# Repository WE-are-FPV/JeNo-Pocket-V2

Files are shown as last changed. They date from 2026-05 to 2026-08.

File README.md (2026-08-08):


> [!NOTE]
> Current version : **2.1.0** (read [changelog](#changelog) for details)

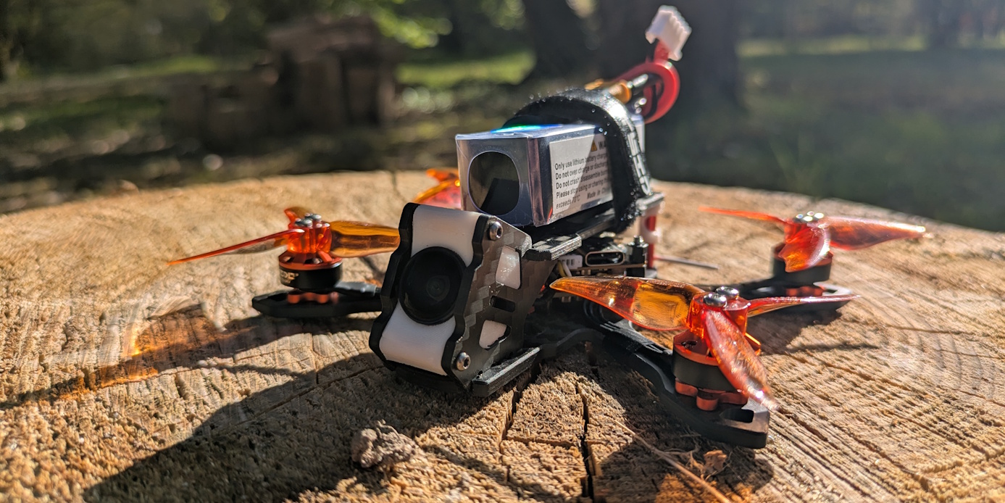
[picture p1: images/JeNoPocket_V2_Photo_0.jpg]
JeNo Pocket V2 - In the hand


# JeNo Pocket V2 2.5"
***2.5" drone FPV frame compatible with Air Unit O4 Lite (or any Nano camera), designed for Freestyle, Freeride and Cinematic.***

> [!NOTE]
> Designed in France by members of the [WE are FPV](https://www.wearefpv.fr/) community, the JeNo is already flown by hundreds of pilots and is now being sold by [Drone FPV Racer](https://www.drone-fpv-racer.com/recherche?controller=search&s=JeNo+5.1+frame&aff=64&id_campaign=13) (affiliate link). The French version of the project is available on [Printables](https://www.printables.com/model/1175339-jeno-pocket-drone-frame). Note that a [3-3.5" version](https://github.com/WE-are-FPV/JeNo-3-3.5), a [5.1-6" version](https://github.com/WE-are-FPV/JeNo-5.1) and a [7-8" version](https://github.com/WE-are-FPV/JeNo-7) of the JeNo exist.

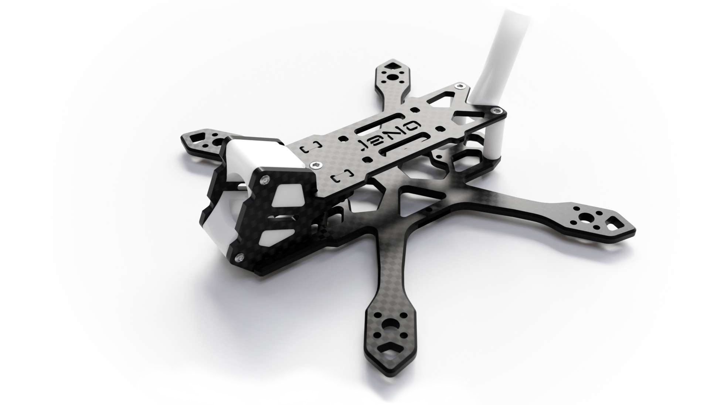
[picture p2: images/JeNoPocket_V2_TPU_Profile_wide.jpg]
JeNo Pocket V2 - 3D render


## Table of contents

* [Key features](#key-features)
* [Presentation](#presentation)
* [Detailed specifications](#detailed-specifications)
* [What’s new compared to the V1](#whats-new-compared-to-the-v1)
* [DJI O4 Wide camera plates](#Camera-plates-dji-o4-wide)
* [Recommended configuration](#recommended-configuration)
* [Versions and files](#versions-and-files)
* [Get it cut !](#buy-it-or-cut-it-)
* [Bill of materials](#bill-of-materials)
* [Building/Assembly guide](#buildingassembly-guide)
* [Inspiration](#inspiration)
* [Tuning, Betaflight Preset](#tuning-betaflight-preset)
* [Blackbox](#blackbox)
* [Videos](#videos)
* [Builds examples](#builds-examples)
* [Authors](#authors)
* [TPU](#tpu)
* [Community (remixes and TPU)](#community-remixes-and-tpu)
* [Changelog](#changelog)

## Key features
- [x] Perfect integration of the DJI **O4 Lite/Wide Air Unit** camera
- [x] Compatible with **O3 lens mods (Khrom’s mod), and O4 Wide lens mods from Flywoo/Runcam**
- [x] **Wide-X** geometry
- [x] Excellent flight **performance**, easy to tune
- [x] **Strong** and **stiff**
- [x] **Frame, standoffs and props are invisible** in the video feed
- [x] **Camera tilt options** : 15, 20, 25, 30 and 35°
- [x] **Bus height options** : 14, 16, 18 and 20 mm
- [x] Designed for: DJI O4 Lite/Wide Air Unit (**+ mods**), Walksnail Avatar/Ascent, Artlynk, HDZero and analog setups
- [x] **Easy to build**, ideal for beginners
- [x] LiPo strap slots
- [x] Compatible with flight controllers featuring a vertical USB port (with the “X-Core” and “Tank” versions)
- [x] **Open source**, of course

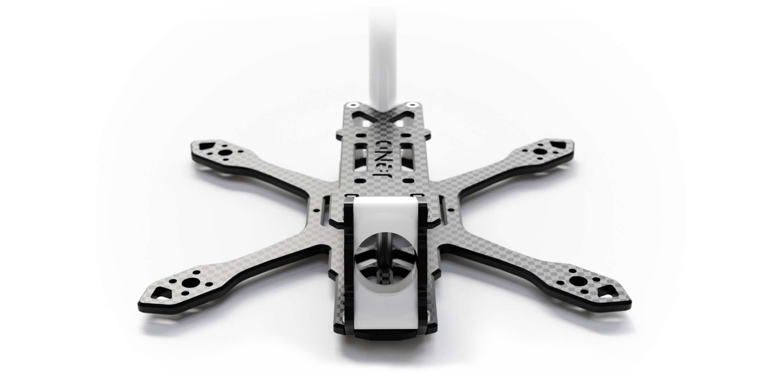
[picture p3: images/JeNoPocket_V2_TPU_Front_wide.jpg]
JeNo Pocket V2 - 3D render Front


## Presentation
In **2025/2026**, we’ve seen a few interesting new developments in the **HD VTX** world: **lens mods** for the DJI O4 Lite, BetaFPV’s **ArtLynk**, and Caddx’s **Ascent**. These evolutions are especially beneficial for compact drones, starting with the 2.5" format.

We are convinced that **2.5" is becoming a major option in FPV**, just like 5" has been for more than a decade, thanks to its many advantages: durability, discretion, lower risk, compact size, reduced manufacturing and consumable costs, ease of building, and more. It is also probably one of the **best options to get started in FPV** !

Following the success of the [first version of the JeNo Pocket](https://github.com/WE-are-FPV/JeNo-Pocket), and with the arrival of [O3 and O4 Wide lens mods](https://www.youtube.com/watch?v=6qGIw0IEMis), which finally give the **DJI O4 Lite a proper FOV**, we wanted to offer the **ultimate version** of the smallest JeNo. Here’s what’s on the menu for the **JeNo Pocket V2** :

* Updated, modern **design**
* Reinforced **durability**
* Compatibility with O4 Lite **lens mods**
* Dedicated camera plates for the new DJI O4 Wide (which replaces the O4 Lite)
* More options, so every pilot can find the setup that suits them:
  * Camera **tilt** options: 15, 20, 25, 30 or 35°
  * Bus **height** options: 14, 16, 18 or 20 mm
  * **LiPo strap** slots
  * Support for flight controllers with **vertical USB port**

Of course, this V2 keeps everything that defines the **JeNo DNA** :

* Carbon camera cage
* High performance and durability
* Completely clear video feed, with no frame or props in view
* Spacious and easy to build
* Open source

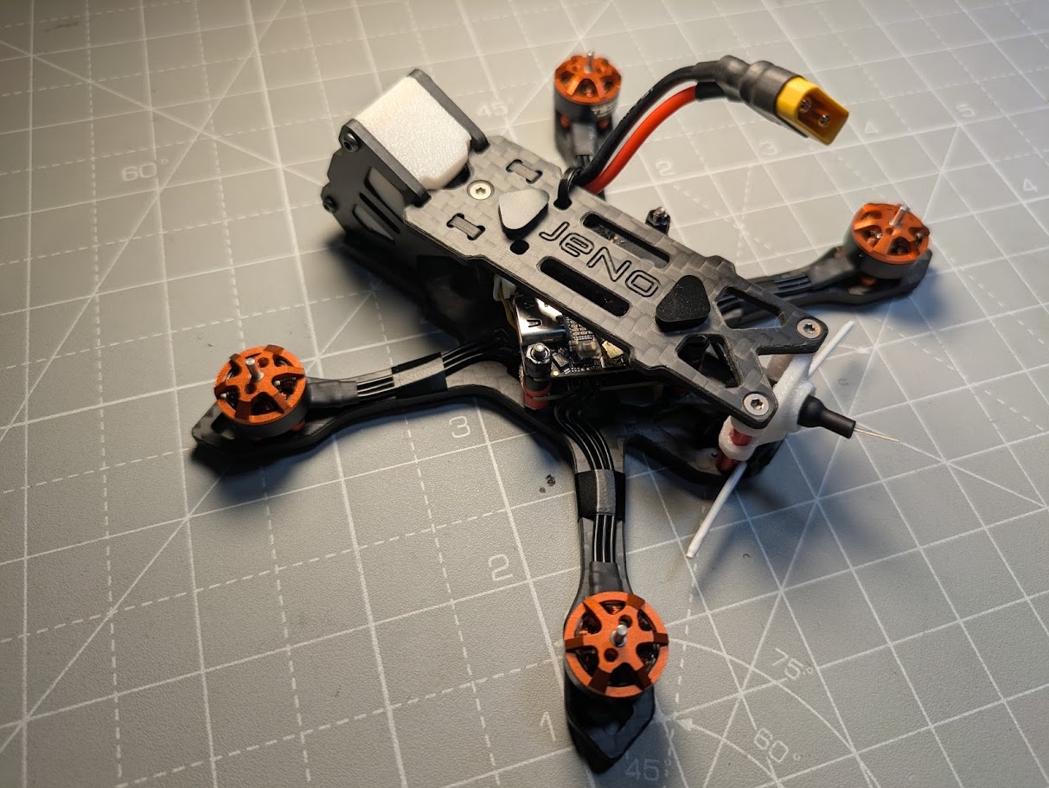
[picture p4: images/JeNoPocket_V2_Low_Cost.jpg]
JeNo Pocket V2 - Back view


This V2 is heavily inspired by [Cam.Traveler](https://www.printables.com/@Cam_Traveler_2489307)’s [JeNo 25](https://github.com/WE-are-FPV/JeNo-Pocket), which itself was inspired by the [JeNo Pocket](https://www.printables.com/model/1175339-jeno-pocket-drone-frame) and [JeNo Fit 3"](https://github.com/WE-are-FPV/JeNo-Fit-3-3.5). Huge thanks to him for his work and for sharing it. Once again, this shows the benefits of open source, where everyone gets to benefit.

## Detailed specifications

|||
| :--- | :--- |
| **Geometry** | **Wide-X** | 
| **Props size** | 2.5" | 
| **Weight** | **X-Core : 25 g**, **Classic : 27 g**, **Tank : 30 g** (with screws) | 
| **Body height** | 14/16/18/20 mm | 
| **Bottom plate** | 3 mm | 
| **Top plate** | 2 mm | 
| **Camera plates** | 2 mm | 
| **Motors mounting** | 9 mm | 
| **Camera** | 14 mm (Nano), O4 Lite and mods, **Clear FOV**. |
| ** Camera tilt** | 15/20/25/30/35° |
| **Main stack** | 25.5 mm x 25.5 | 
| **Back stack** | RX area. 13 mm x 13 mm | 
| **Supported VTX** | Analogic, **DJI Air Unit O4 Lite/Wide (+mods)**, WalkSnail Avatar/AScent, HDZero, ArtLynk… | 
| **Strap passage** | Yes | 

## What’s new compared to the V1

### Redesign and durability

Since the [JeNo Fit 3"](https://github.com/WE-are-FPV/JeNo-Fit-3-3.5), we’ve been trying to move away from the standard stack-area design, with its classic side “spikes”, and adopt **more harmonious shapes** instead. This improves both the look and the **durability**, with wider arm bases that are therefore stronger and more rigid.

Here is an overview of the main differences between the V1 and the V2. The center patterns have been removed for this comparison, so we can focus on the main structure.

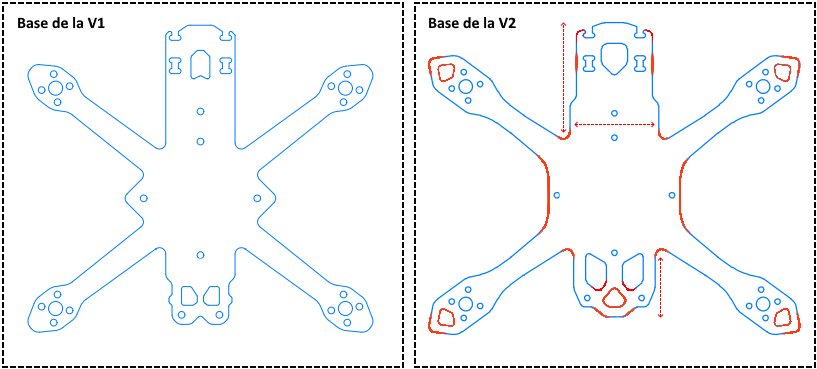
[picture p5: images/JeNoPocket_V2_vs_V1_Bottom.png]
JeNo Pocket V2 - V1 vs V2


The red areas highlight the main changes. Beyond the **more visually appealing design**, the arms appear shorter — and they actually are! Removing the side spikes in favor of a direct junction between the arms and the bus **significantly reinforces the arms**.

There are also a few other improvements worth highlighting:

* Better **motor protection** at the end of the arms
* **The front** of the bottom plate has been **widened and shortened for better durability**. There is also more material between the slots for the camera plates and the edge of the frame.
* **The rear** has also been shortened
* Mounting support for a T-style antenna
* As we will see later, cutouts are also provided for flight controllers with a **vertical USB port**.

The following image shows an overlay of the V1 and V2 to better illustrate the differences.

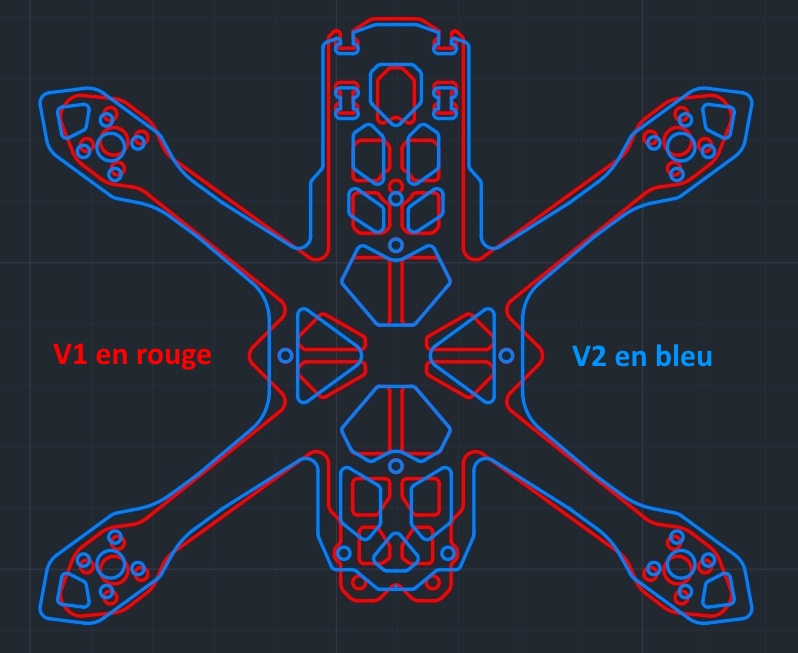
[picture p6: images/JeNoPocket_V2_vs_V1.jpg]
JeNo Pocket V2 - V1 vs V2 over


### "À la carte" bottom plate options

We offer **3 versions** of the bottom plate, all based on the improvements mentioned above.

The **V2 “Classic”** bottom plate is the direct evolution of the **V1** : it features a carbon cross in the center, ensuring good rigidity across all axes. Like the V1, it also **does not include** a cutout for flight controllers equipped with a **vertical USB port**.

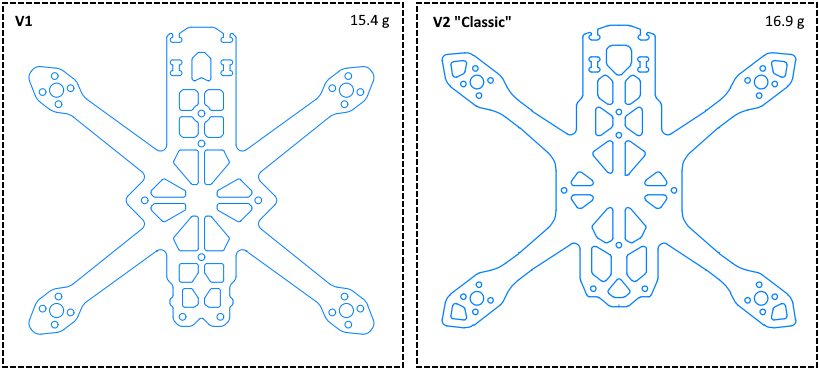
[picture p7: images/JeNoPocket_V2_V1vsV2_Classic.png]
JeNo Pocket V2 - V1 vs V2 Classic


*Two other versions** are also available, both **compatible** with flight controllers equipped with a **vertical USB port** :

* **V2 “X-Core”** : this is the optimized version of the JeNo Pocket V2. Lighter than the “Classic” and more durable than the V1, it is characterized by a **carbon X in the center**, following the diagonals of the arms. **Ideal with lightweight props** such as the Gemfan 2520. It is less tolerant of heavy props that generate a lot of vibrations, such as the Avan Rush.

* **V2 “Tank”** : with its **wider arms** and “solid” carbon layout, this is the **stiffest and most durable** of the 3 versions. We did not call it V2 “Bando” because, in absolute terms, all 3 versions remain strong enough for that kind of flying.

At **4.7 g heavier** than the **“X-Core”** version, it is also **more tolerant** of heavy or high-pitch props during hard full-throttle punches.

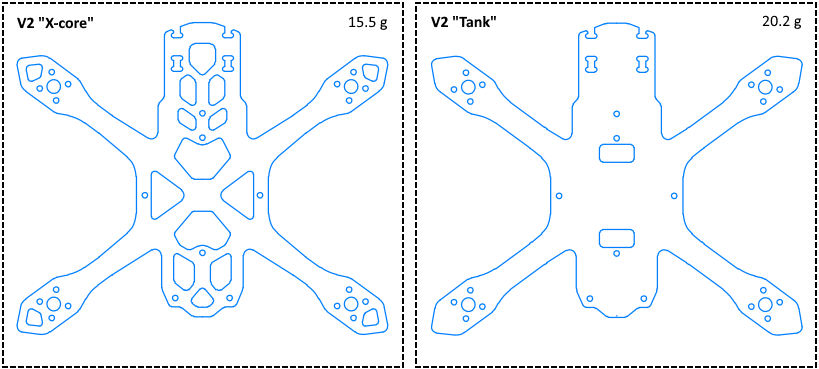
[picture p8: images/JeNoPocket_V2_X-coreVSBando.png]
JeNo Pocket V2 - X-Core vs Tank


Example build with a flight controller equipped with a vertical USB port:

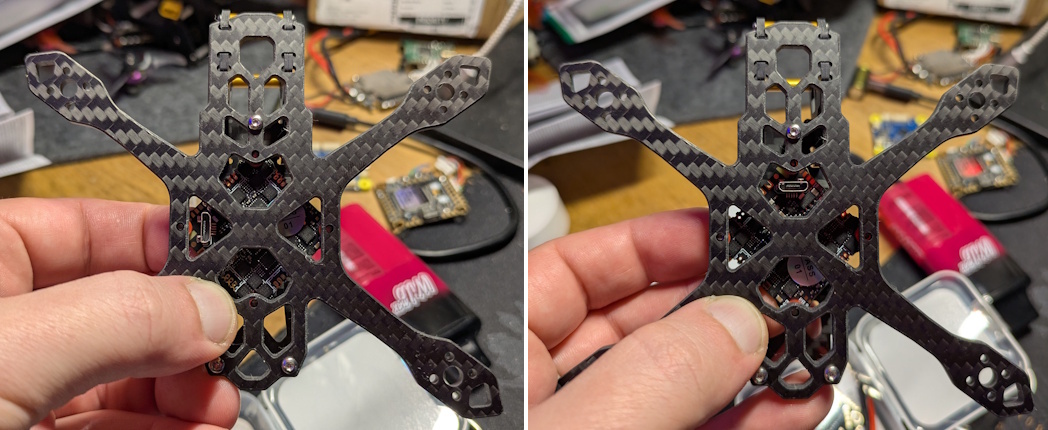
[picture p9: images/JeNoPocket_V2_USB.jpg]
JeNo Pocket V2 - vertical USB


### Customizable camera plates : height and tilt

The **single bus height** of the **V1**, 20 mm, was convenient because it was spacious and even allowed for a Naked Vista build, but some pilots prefer a more **low-profile** bus. It is now possible to **choose the height** :

* **14 mm** : very low-profile, but be careful, the build will be more difficult
* **16 mm** : a good compromise, making the build easier while staying relatively low profile — Nochamo’s preference
* **18 mm** : allows for an easy build without going all the way up to 20 mm — Jérôme’s preference
* **20 mm** : still available for maximum space and Naked Vista compatibility

We recommend the two intermediate versions: 16 or 18 mm.

Camera tilt is now also optional: the camera plates are available in **15, 20, 25, 30 or 35°**.

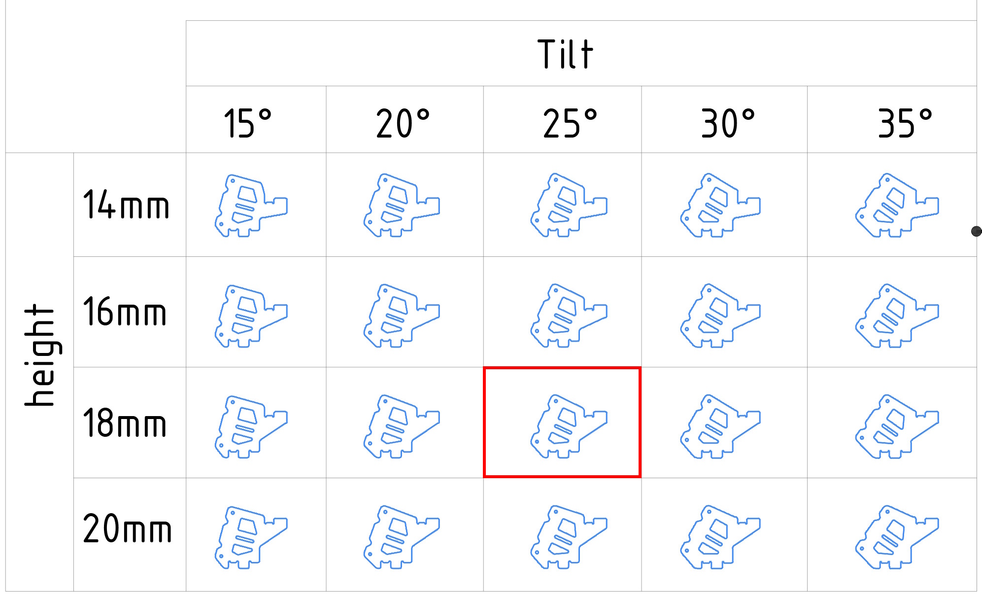
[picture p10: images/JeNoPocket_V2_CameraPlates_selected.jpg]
JeNo Pocket V2 - Camera plates


As an example, in the image above, the version highlighted in red is the one to choose for an 18 mm bus height and a 25° camera tilt.

### Camera plates DJI O4 Wide

The **JeNo Pocket V1 and V2** were designed, in part, around the **DJI O4 Lite**. Unfortunately, it is **no longer available** and has been replaced by the **DJI O4 Wide**. While the VTX itself is identical, the camera—particularly the lens and its mounting system—is different.

The larger size of the new DJI O4 Wide camera required us to design a new set of **dedicated** camera plates.

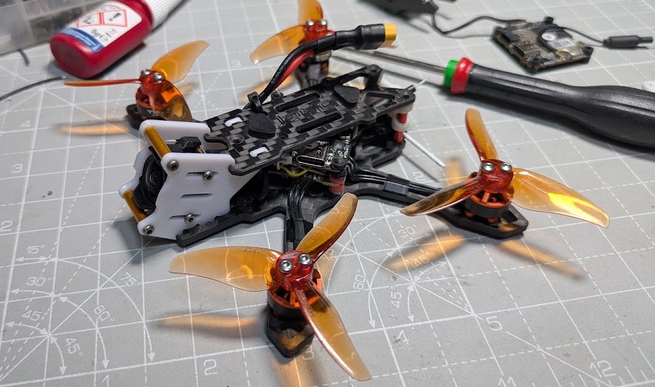
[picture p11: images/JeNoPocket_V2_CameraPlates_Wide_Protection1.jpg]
JeNo Pocket V2 - DJI O4 Wide


We could have replaced the standard camera plates with these new ones, but we chose not to compromise the design for all the other cameras just to accommodate the constraints of the O4 Wide. You will therefore be able to choose between **two types of camera plates** for the JeNo Pocket V2:

* **Standard** model: this is the original version and the one we recommend for **ALL** cameras **except** the DJI O4 Wide camera. Even when using a DJI O4 Lite with an **O3 lens mod**, this is the model you should choose.
* **DJI O4 Wide** model: this version should **only** be used with the DJI O4 Wide. Its main advantage is that it does not require any TPU mount: the camera is screwed directly onto the camera plates. No modification or workaround is needed—it can be installed straight out of the box. The downside is that the plates are slightly larger and consist of separate left- and right-hand parts.

The illustration below will help you visualize the difference in size.

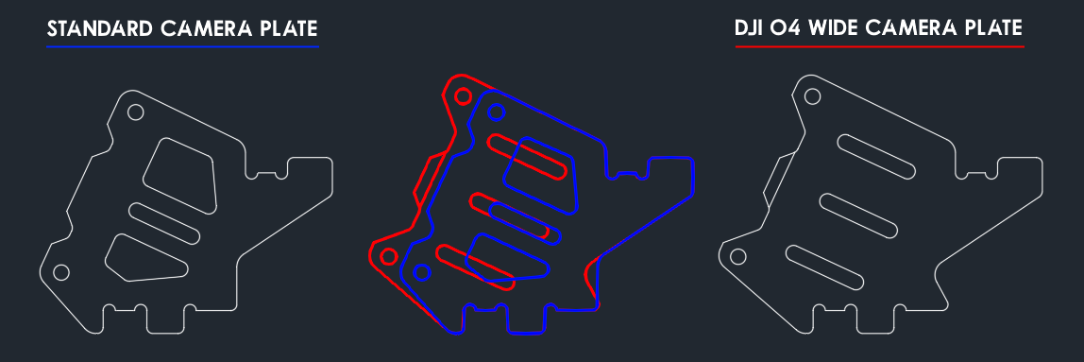
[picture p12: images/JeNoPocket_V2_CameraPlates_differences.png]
JeNo Pocket V2 - DJI O4 Wide differences


To provide the **best possible protection** for the DJI O4 Wide lens while keeping its **FOV** completely **unobstructed**, we had to add **chamfers** to the central section. This means using two different, mirrored plates for the left and right sides.

We would like to draw **carbon manufacturers’** attention to the precision of these chamfers. They are **essential** to allow the camera to be positioned as far back as possible.

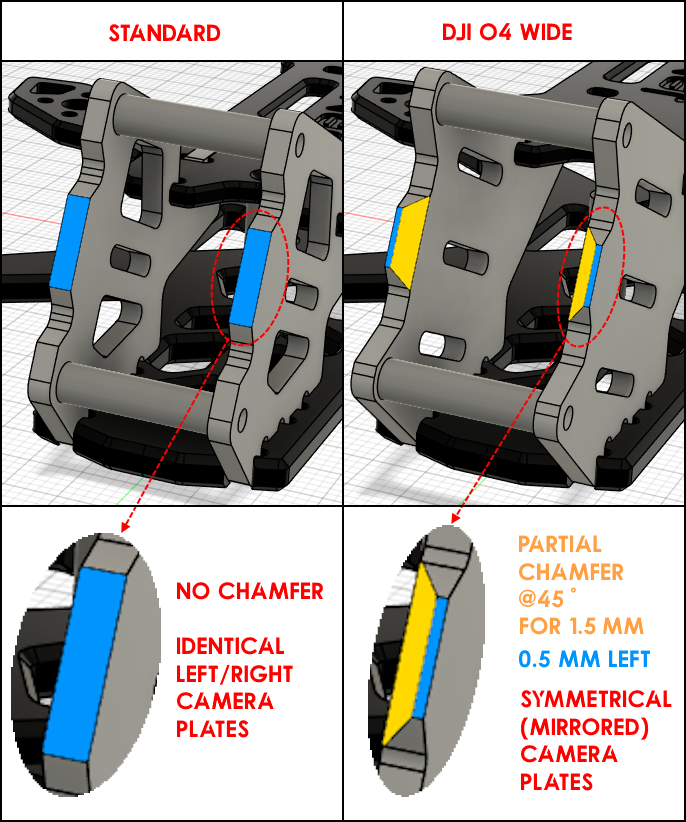
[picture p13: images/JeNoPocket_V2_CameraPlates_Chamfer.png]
JeNo Pocket V2 - DJI O4 Wide chamfers


The camera must be moved forward precisely to the beginning of the chamfer, as shown in the photo below.

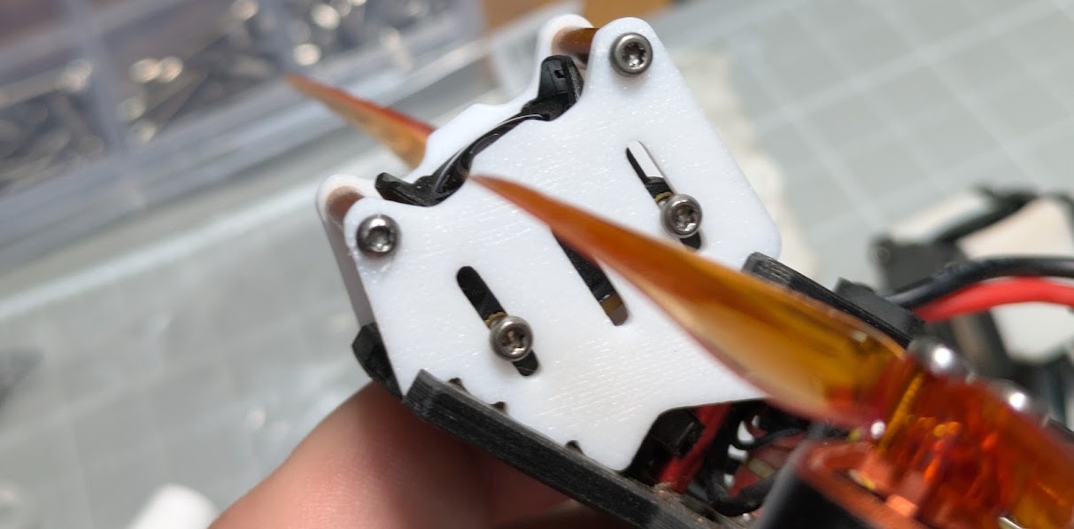
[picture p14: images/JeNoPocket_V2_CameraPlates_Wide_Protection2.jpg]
JeNo Pocket V2 - DJI O4 Wide placement


This ensures optimal protection.

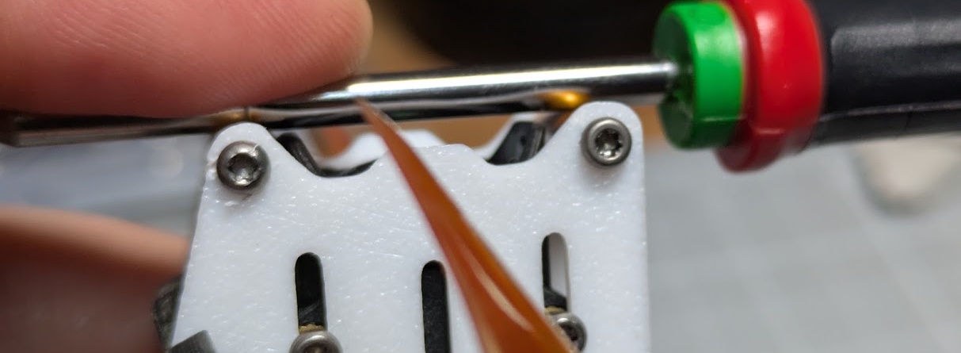
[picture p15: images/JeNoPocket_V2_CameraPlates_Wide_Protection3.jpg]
JeNo Pocket V2 - DJI O4 Wide placement


### Top plates

The top plate remains fairly simple, with the addition of **slots for a LiPo strap**.

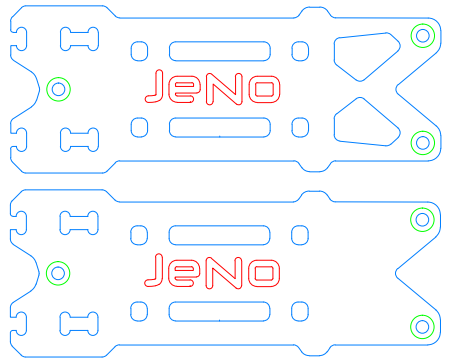
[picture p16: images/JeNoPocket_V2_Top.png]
JeNo Pocket V2 - Top plate


The **two small holes** above and below the “J” are intended to secure the **pigtail** with a **zip tie**.

Given the size of the frame, the “JeNo” engraving is quite fine. If your carbon cutter is not able to machine the logo as a **pocket**, it is still possible to **engrave only the outline** — it also looks very nice.

The space on both sides of the logo can be used to install small **LiPo pads**.

JeNo Pocket V2 - LiPo Pads

A **reinforced version** of the top plate is also available for the **“Tank”** version.

### Camera mounts

For standard **Nano-sized** cameras, with one screw hole on each side, mounting is done directly through the central rail of the camera plates, allowing you to adjust the camera setback as needed.

| Standard nano camera | O3 Lens Mod |
| :---: | :---: |
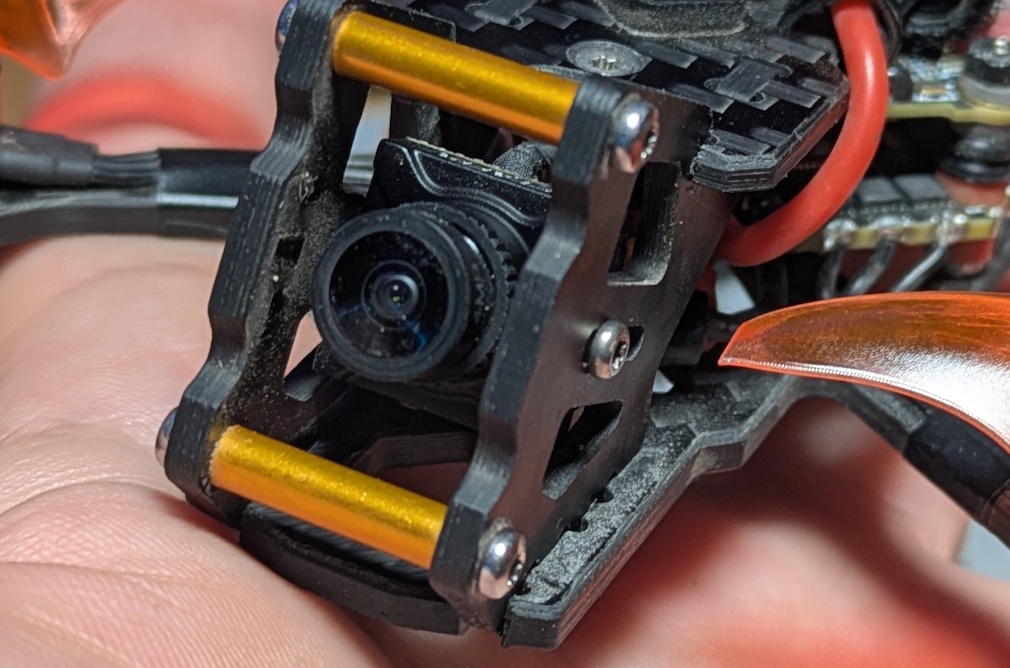
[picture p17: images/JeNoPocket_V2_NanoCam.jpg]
JeNo Pocket V2 - Standard nano camera
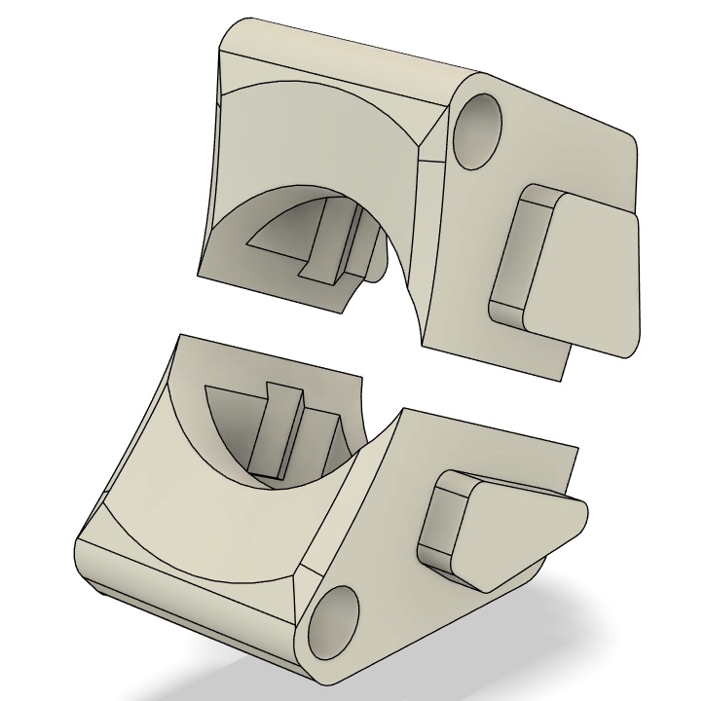
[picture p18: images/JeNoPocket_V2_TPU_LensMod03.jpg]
JeNo Pocket V2 - O3 Lens Mod
|  |  |

For the O4 Lite camera, we designed two-piece TPU mounts that wrap around the camera and are locked in place by the camera plates. Three TPU mounts are available:

A standard version for the unmodified O4 Lite camera
A version for the O3 lens mod — the best conversion currently available
A version for the Flywoo/Runcam O4 Wide lens mod

To get a **fully unobstructed FOV**, move the lens about one millimeter forward past the TPU, as shown in the image above. Conversely, for more protection, you can move the camera very slightly backward, at the cost of very minor vignetting.

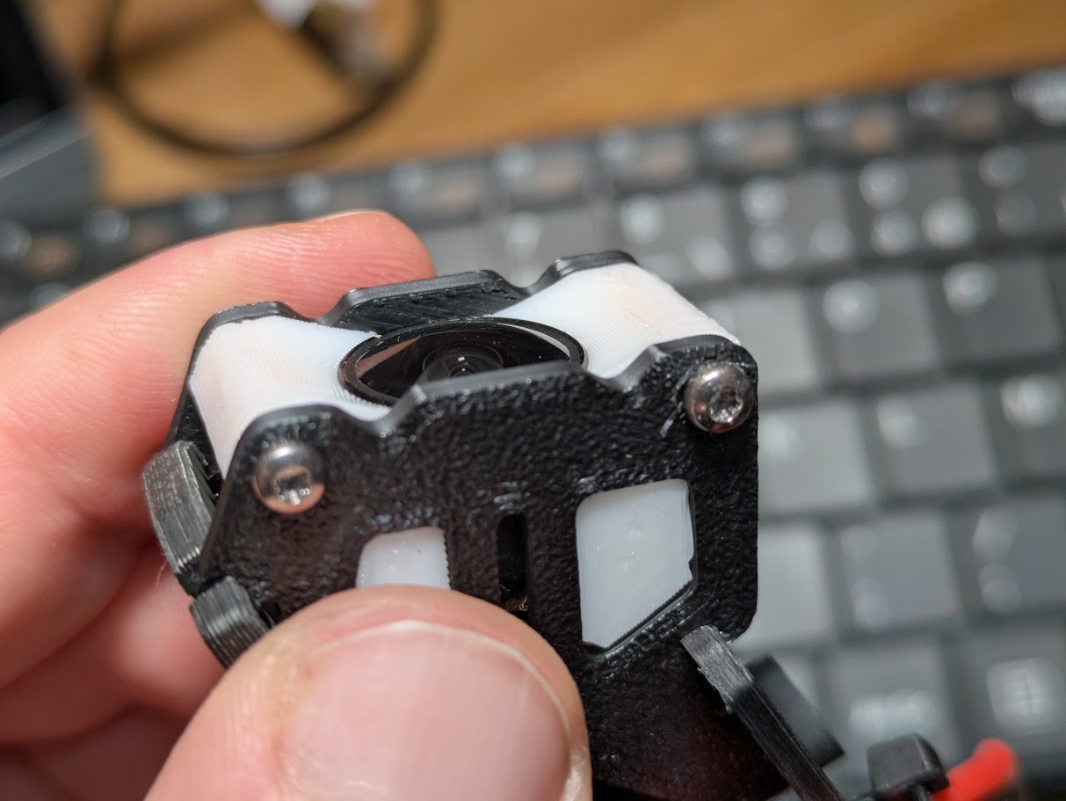
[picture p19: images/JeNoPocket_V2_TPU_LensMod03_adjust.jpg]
JeNo Pocket V2 - O4 Lite mods


These TPU parts are designed to integrate perfectly with the carbon. However, depending on cutting tolerances and leftover TPU support material, a few small adjustments with flush cutters may be required for the TPU to fit properly.

## Recommended configuration

Different approaches are possible, from ultra-light to mini-rocket, depending on your hardware choices.

### Motors

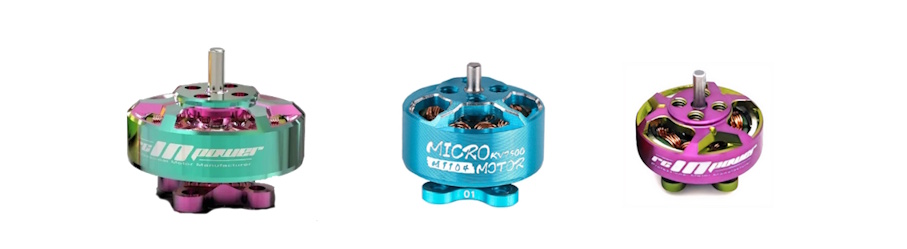
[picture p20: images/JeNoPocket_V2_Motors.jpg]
JeNo Pocket V2 - Motors


| **Size** | **Stator volume** | **Recommended KV (2S)** | **Recommended KV (3S)** |
| :---: | :---: | :---: | :---: |
| 1202 | 226 mm³ | ~8000 | ~6000 |
| 1103 | 285 mm³ | ~8000 | ~6000 |
| **1203** | **339 mm³** | **~8000** | **~6000** |
| **1104** | **380 mm³** | **~8000** | **~6000** |
| **1303** | **398 mm³** | **~8000** | **~6000** |
| 1204 | 452 mm³ | ~8000 | ~6000 |
| 1105 | 475 mm³ | ~8000 | ~6000 |

2S motors can also be used on 3S thanks to **Betaflight’s Motor Limit** feature. In fact, this is probably the best approach: choosing motors around **7500–8000 KV** allows you to run them on both 2S and 3S.

These small motors, such as the **RCInPower** 1203 8000KV or **BetaFPV** 1104 7500KV, are still quite expensive despite their size. A low-cost option is available from [**YSIDO** with their 1104 7500KV motors](https://fr.aliexpress.com/item/1005005729701162.html), which can usually be found for around €20–25 for a set of 4. For bando flying, they probably won’t be the most durable option, but for freestyle, they do the job very well.

### Lipos

We recommend **2S or 3S lipos** as indicated in the table above, although 4S is also an option.

**2S ~550 mAh** lipos are a good compromise, or **3S ~450 mAh**. For maximum flight time, **3S ~550 mAh** lipos are still perfectly viable.

Small 2S ~450 mAh lipos are possible with a very light setup and small motors, but the impact on flight time and sag may become noticeable.

In any case, we strongly recommend **Dogcom 2S and 3S 560 mAh** lipos, as they have shown the best performance by far.

<p align="center">
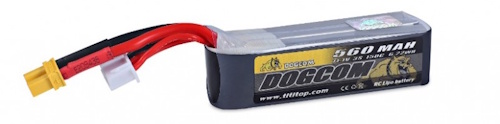
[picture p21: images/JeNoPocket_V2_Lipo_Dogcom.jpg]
  
</p>

Depending on the lipos, during a freestyle flight outdoors in cold weather (~5°C), flight times can range from **2 minutes** (BetaFPV 2S 450 mAh) to **5 minutes** (Dogcom 3S 560 mAh)! You can even hope to reach **7 minutes** with a smooth flight using these same lipos.

### Props

We tested many props from **Gemfan, HQ and Emax** for freestyle flying. The props we recommend are the **Gemfan Hurricane 2520-3** and the **HQ 2.5x1.9x3** : light, responsive and precise. They work perfectly with all bottom plate versions and make a perfect combo with the **“X-Core”** version: it is lightweight and flies very well.

The **Emax Avan Rush 2.5"**, along with other heavier or higher-pitch props, are more “brutal” due to their very **unusual profile** and **higher weight**. This is not an issue for freestyle flying, but during sustained full-throttle punches, vibrations may appear on the “X-Core” version. The **“Classic” and “Tank”** versions absorb them well.

[Here is an example of a full-throttle punch followed by freestyle flying](https://youtu.be/E_eKk1bxeOk) in 3S on the **“X-Core”** version with these **Avan Rush 2.5"**, to illustrate the behavior with these props.

We did not want to exclude them from the recommended props for the JeNo Pocket V2 for 3 reasons:

* They are the **most durable props** available. You almost never need to replace them, which is an important point, especially with T-Mount props, which are often tedious to change.
* The vibration issue does not exist on the **“Tank”** version and is anecdotal on the **“Classic”** version.
* On the “X-Core” version, it only appears during full-throttle punches. It is not a deal-breaker, but the Gemfan 2520 simply fly much better.

> [!TIP]
> **Gemfan 2520 →** ideal for **all versions** of the JeNo Pocket V2

> [!TIP]
> **Emax Avan Rush →** we recommend the **“Classic”** or **“Tank”** versions for better flight behavior, especially during full-throttle punches.

### FC, ESCs and RX
Here, you’ll have plenty of choices, as the range is very diverse. The main recommendation is to go for an **FC AiO** with ESCs that can deliver **20A**, to be on the safe side, although theoretically, 15A should be sufficient.

The O4 Lite can be powered **directly from the lipo** if you’re using 2S or 3S. For higher voltages, you'll need an FC with a BEC capable of delivering at least 10W for the O4.

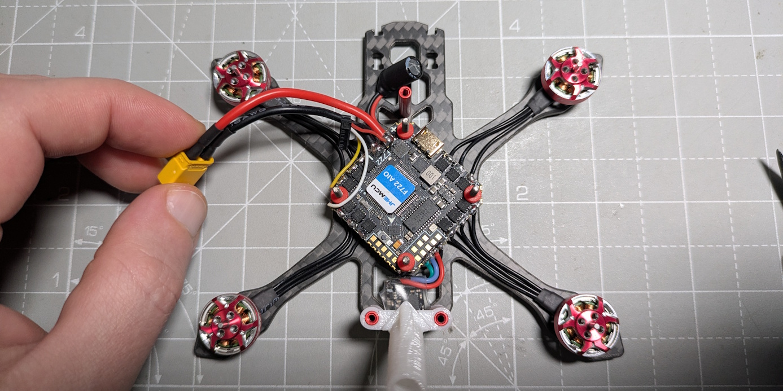
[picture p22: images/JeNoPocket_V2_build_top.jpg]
JeNo Pocket V2 - Top view


Having experienced many unreliable AiOs that didn’t meet the advertised specifications, we recommend opting for **proven hardware**.

Choosing an FC with an **integrated RX** can be a good option to save weight. When they feature a copper antenna, the range is generally quite limited. An **external RX** will often be a better option for range.

Those equipped with a flat antenna or, even better, a ceramic antenna, will offer a good balance of range while minimizing weight gain.

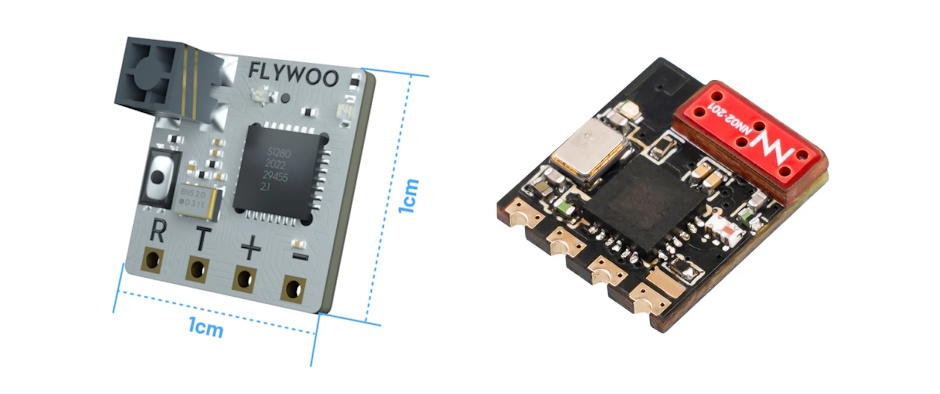
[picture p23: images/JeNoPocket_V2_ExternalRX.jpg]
JeNo Pocket V2, RX options


**Affordable and proven AiO recommendations :**

* **[JHEMCU GHF722AIO-HD 40A](https://fr.aliexpress.com/item/1005004940172936.html) :** almost overkill for a 2.5", but still a solid option with lots of positive feedback. We even use it on our 3.5" builds. However, you will need to add an external RX.

* **[JHEMCU GHF435AIO V2 20A](https://fr.aliexpress.com/item/1005007942847361.html) :** probably the perfect AiO for the JeNo Pocket. Its F435 is roughly equivalent to an F722, it is cheaper, and it also comes with an onboard RX! And this is a real RX, not an SPI receiver. It can therefore be used and flashed like a standalone RX. The cherry on top: it has a µ.FL connector, allowing you to use a proper antenna and therefore get maximum range. On this FC, the USB connector is vertical, so the **“X-Core” or “Tank”** version is required.

The **capacitor** is generally not required for 2S and 3S builds, but if you choose to use one, a **220 µF 25V** will do the job and can be placed either at the front standoff or at the back.

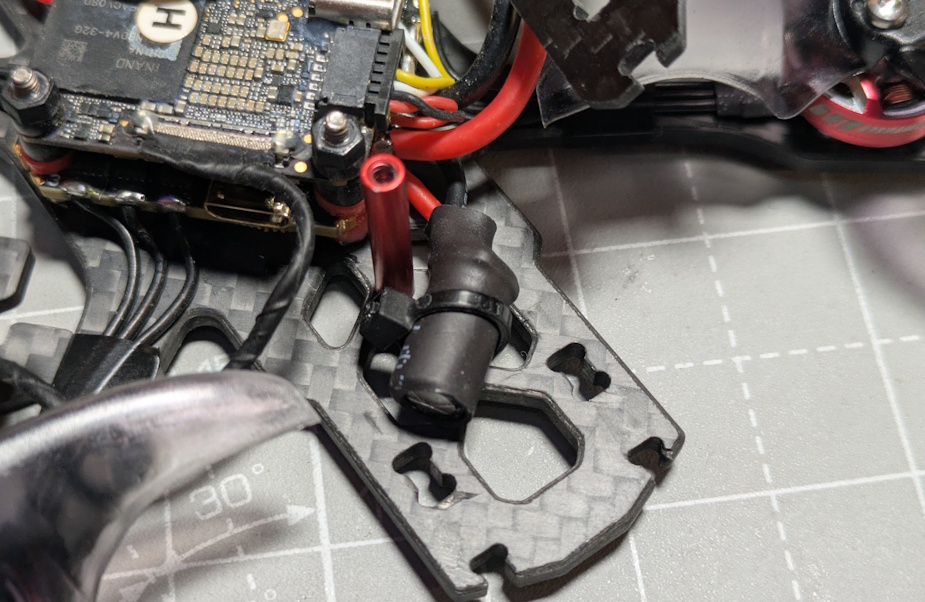
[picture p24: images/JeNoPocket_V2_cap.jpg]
JeNo Pocket V2, Capacitor


As for the **XT30** pigtail, **18 AWG** cable is a good compromise.

## Versions and files

### Versioning
You will find the **current version** of the frame at the beginning of the description and the full [history of modifications](#changelog) at the end of the page.

We strongly recommend always cutting the latest version to ensure you benefit from the most recent optimizations.

The version **number format** is as follows :
```
<Major versions>.<Minor version>.<Revision>
ex : 1.3.2
```

* **Revision :** This number is incremented in the case of minor modifications with no significant impact.
* **Minor version :** This number is incremented for minor modifications that may potentially break compatibility with certain TPU parts.
* **Major version :** This number is incremented for significant modifications that break compatibility at the carbon level.

**Note :** If you develop TPU parts for the JeNo, be sure to specify the version they are compatible with.

### Files management
To simplify things, we have reorganized the file structure. The files are now divided into **five groups** :

* **01-FRAME :** Contains **models** describing the **frame** in DXF, STEP, and STL formats for the current version. Also contains a PDF file which is a reformatted version of the DXF.
* **02-TPU :** Contains **TPU models** for the current frame version in STL format.
* **03-FRAME-HISTORY :** Contains previous versions of the frame.
* **04-TPU-HISTORY :** Contains TPU models that are no longer compatible with the current version.
* **OTHER-FILES :** Contains documentation files, including the assembly manual and a description.

## Get it cut !

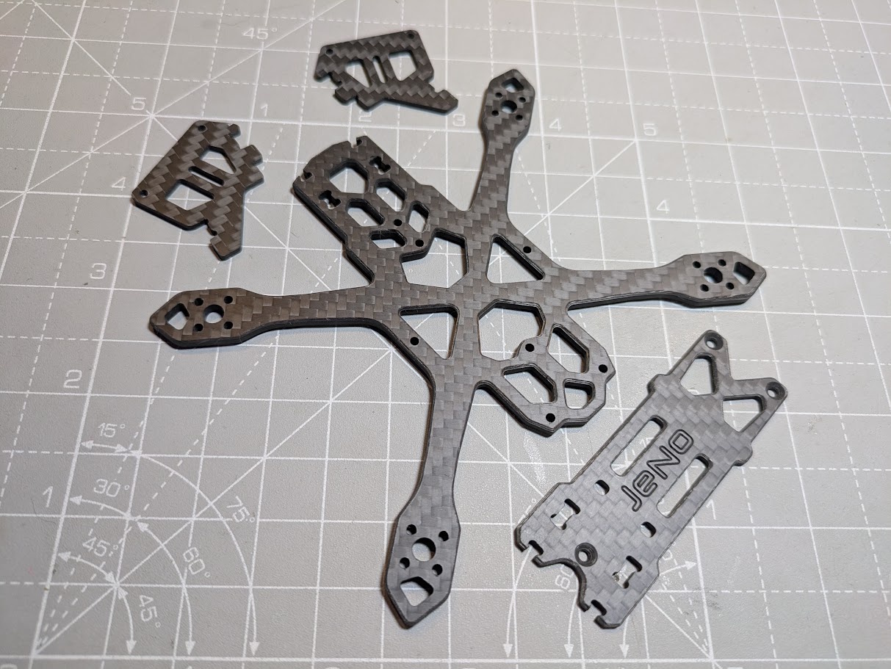
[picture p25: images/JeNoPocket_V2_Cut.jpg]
JeNo Pocket V2, cut


The JeNo Pocket V2 is available at [FPV CNC Drone](https://fpvcncdrone.com/).

The ["01-FRAME"](https://github.com/WE-are-FPV/JeNo-Pocket-V2/tree/main/01-FRAME) folder contains all the files you need to get it **cut**. .DXF and .STEP files are available.

The bottom plate must be cut from 3 mm thick carbon fiber. The top plate and camera plates should be cut from 2 mm carbon fiber.

By default, we recommend adding **chamfers everywhere, except on the camera plates**.

**One last point :** carbon cutters generally use carbon sheets made of fiber layers oriented at 0° and 90°. To achieve the best arm stiffness, the bottom plate should be **oriented at 45°** during cutting. This is something they are usually very familiar with, but we prefer to mention it.

## Bill of materials

In addition to the carbon fiber, you will need the following hardware to complete the assembly of the frame.

**Standoffs**

Important note: M2 standoffs come in two diameters: 3.5 mm and 4 mm. **Make sure to use 3.5 mm diameter standoffs** (you can optionally keep a 4 mm diameter for the central standoff.).

If you machine or manually shorten the standoffs, make sure to precisely match the bus height required for your camera plates.

| Quantity | Description | Details |
| :---: | :--- | :--- |
| **3** | **M2** standoffs, **3.5 mm diameter**. Available in 14, 16, 18 or 20 mm, depending on the selected bus height. | for the body |
| **2** | **M2x14mm** standoffs **(3.5 diameter)** | for the camera |

**Stack materials**

Titanium is lighter, but it will tend to bend over time after repeated hard crashes. This is even more noticeable with taller stacks.

| Quantity | Description | Details |
| :---: | :--- | :--- |
| **4** | **M2x20mm** screws, depending on the selected bus height: 14 mm → M2x16, 16 mm → M2x18, 18 mm → M2x20, 20 mm → M2x20 | for the stack |
| **8** | **M2** nylon nuts for the stack screws (4 nuts for the base, 4 nuts on top) | for the stack |

**Frame materials**

Don’t hesitate to apply a small amount of threadlocker to the screws to reduce the risk of them coming loose, which is fairly common on small, high-powered builds using M2 hardware.

| Quantity | Description | Details |
| :---: | :--- | :--- |
| **3** | **M2x6-8 mm** countersunk screws | for the top plate |
| **3** | **M2x8-10 mm** screws | for the bottom plate |
| **4** | **M2x6 mm** screws (titanium if possible) | for camera plates |

**Additional materials**

| Quantity | Description | Details |
| :---: | :--- | :--- |
| **12-16** | **M2x5mm** screws if there is NO arm protection between the screw and the motor, otherwise, **M2x6mm**. To save **weight**, you can use only **2-3 screws per motor**. | for the motors |

## Building/Assembly guide

### Build
The assembly of the frame is straightforward :

<p align="center">
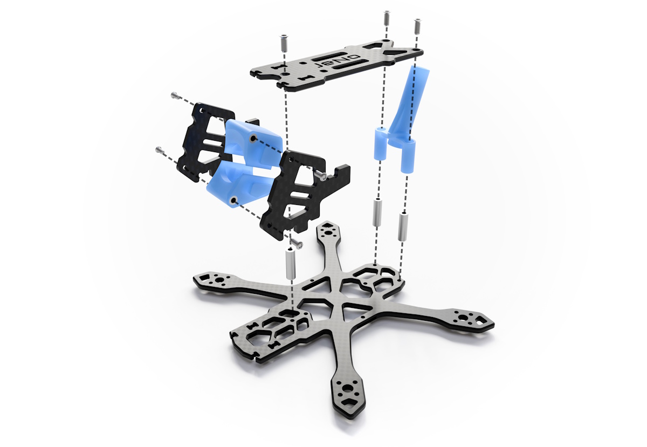
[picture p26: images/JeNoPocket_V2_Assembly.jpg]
  
</p>

[Complete build tutorial (French)](https://www.youtube.com/watch?v=vF8HRb9n8Hg)

### Lipo mounting

Two areas are provided on the top plate, on each side of the logo, to stick two small LiPo pads if you want to use them. We recommend using 1.5 mm thick **LiPo pad** to keep the weight down.

**12–14 cm straps** will work very well for 2S and 3S LiPos from 450 to 560 mAh. Note that the top plate now includes dedicated strap slots.

Finally, **two small holes** on the top plate allow you to **secure the pigtail** with a **zip tie** in case the LiPo gets ripped off:

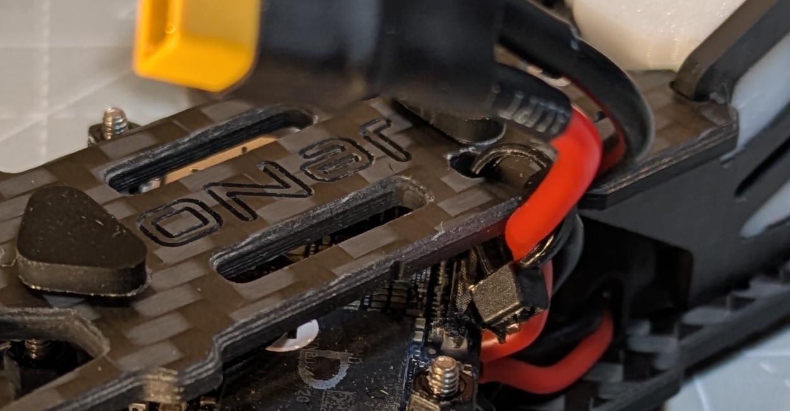
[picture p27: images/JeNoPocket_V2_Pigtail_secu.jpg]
JeNo Pocket V2, pigtail


## Inspiration

The **JeNo Pocket** was initially inspired by its two bigger brothers, the JeNo 3" and 5".

**The rear stack is gone**, as it is no longer needed with the DJI O4 Lite Air Unit. The front section, made of two camera plates, was designed around the O4 Lite camera and its lens mods.

Although the V2 has been completely redesigned, it draws inspiration from [Cam.Traveler](https://www.printables.com/model/1236609-jeno-25-drone-frame-jeno-pocket-custom)’s [JeNo 25](https://www.printables.com/model/1236609-jeno-25-drone-frame-jeno-pocket-custom), which itself was inspired by the [JeNo Pocket](https://github.com/WE-are-FPV/JeNo-Pocket) and [JeNo Fit 3"](https://github.com/WE-are-FPV/JeNo-Fit-3-3.5).

## Tuning, Betaflight Preset

**No built-in preset** for now. AiO behavior can vary quite a lot from one board to another, so we’ll wait until we have more feedback.

However, here is an overview of the first tune used for our test flights, which you can use as a starting point **if your Blackbox logs are clean enough**. Note that we enabled profile switching based on the LiPo cell count.

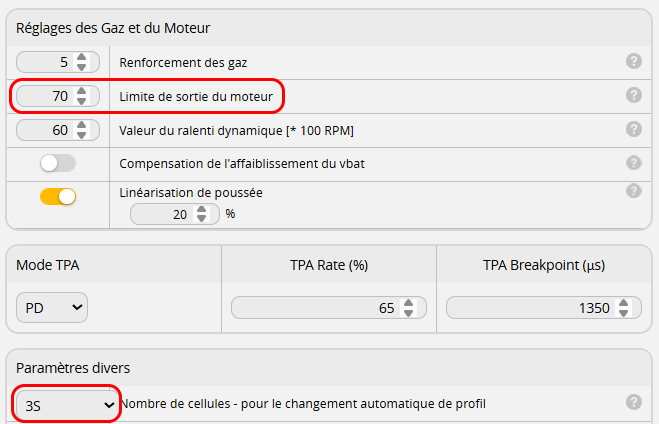
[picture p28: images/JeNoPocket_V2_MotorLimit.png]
JeNo Pocket V2, Cell count


As always, **be very careful** when applying these settings.

**PID profile for 2S :**

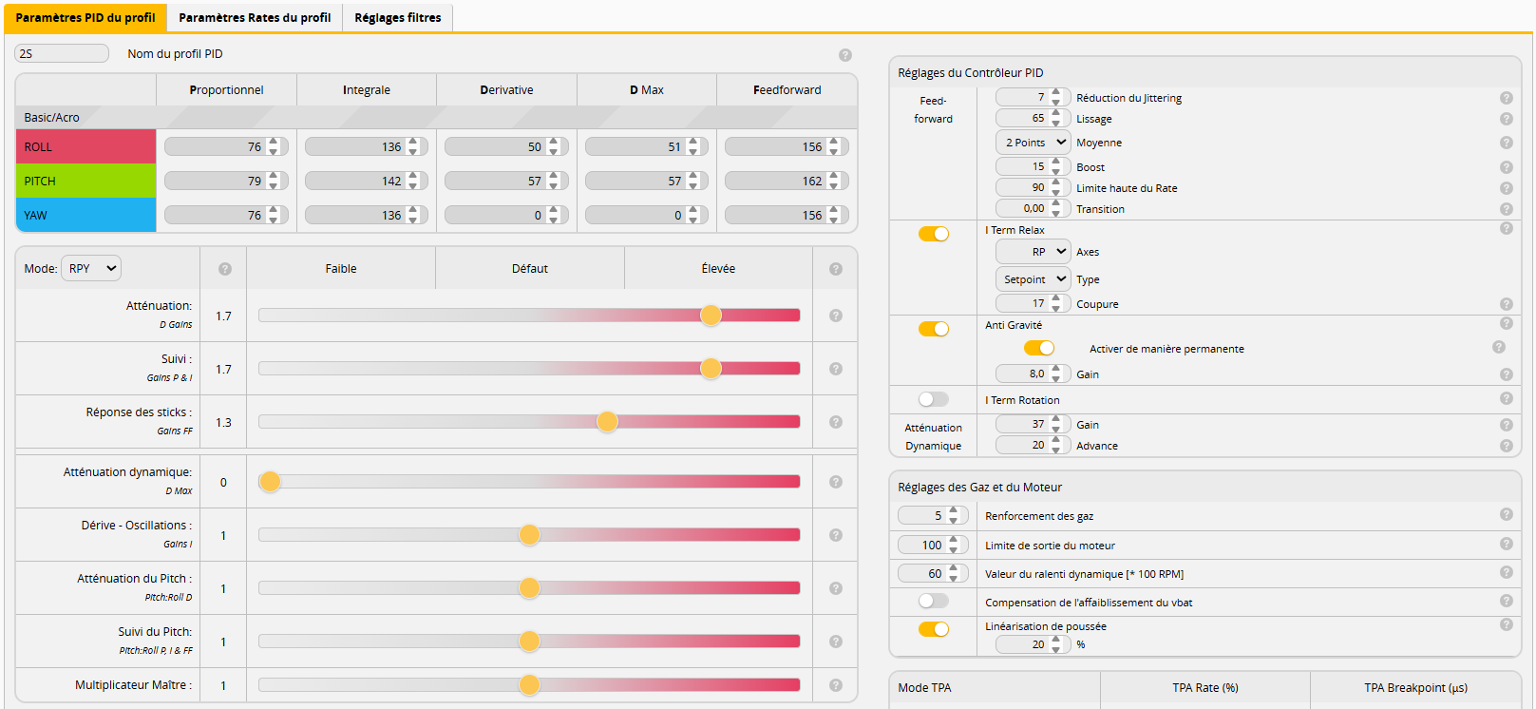
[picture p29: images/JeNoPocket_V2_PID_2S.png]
JeNo Pocket V2 - 2S PID Profile


**PID profile for 3S (8000KV motors limited to 70-75%):**

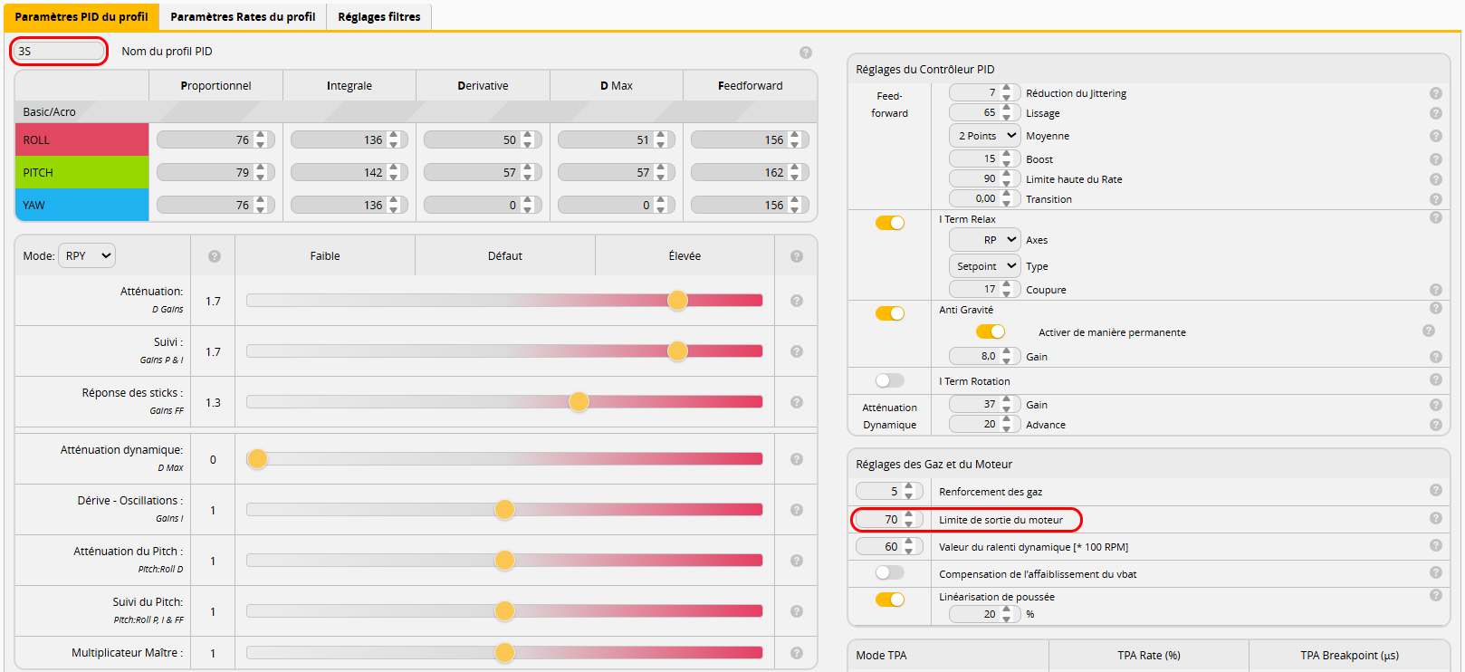
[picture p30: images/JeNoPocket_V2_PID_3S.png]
JeNo Pocket V2 - 3S PID Profile


**Filters :**

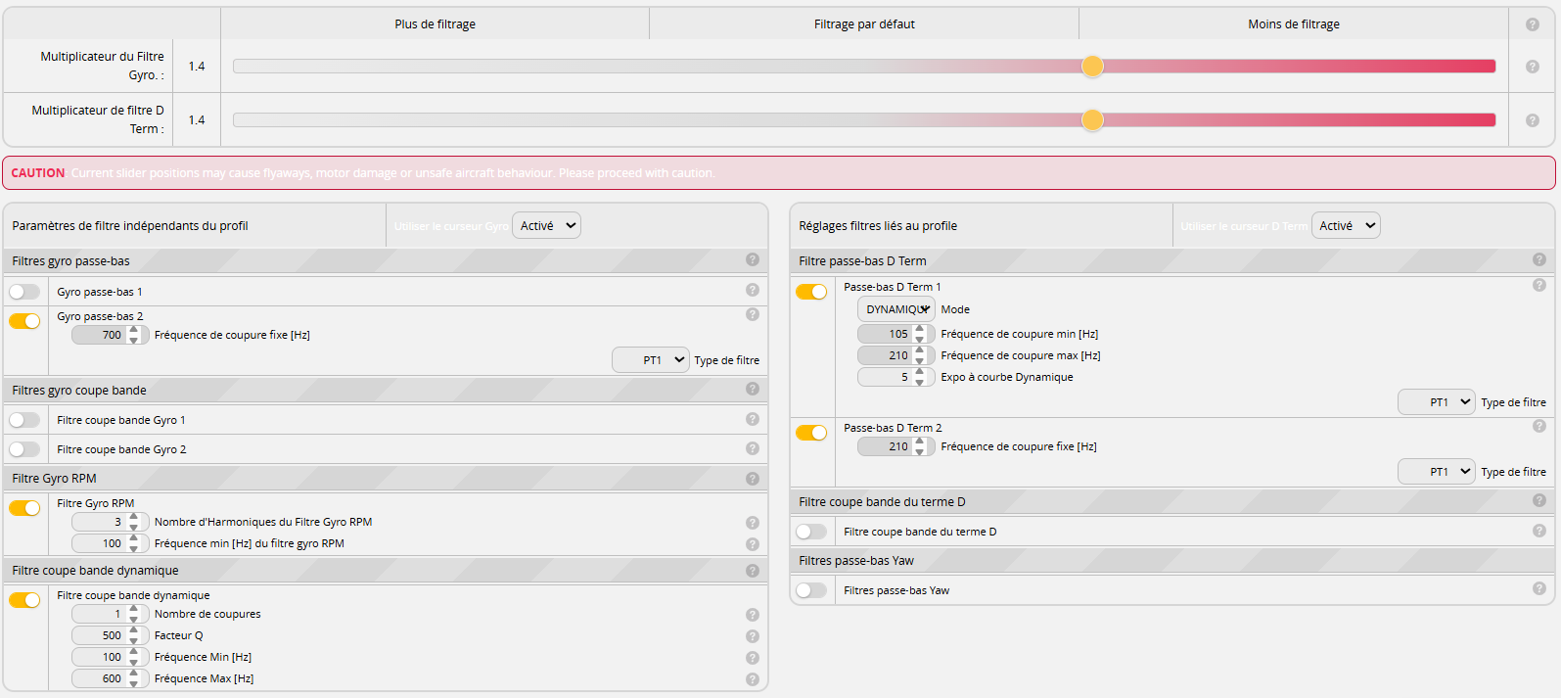
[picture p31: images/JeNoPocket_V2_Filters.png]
JeNo Pocket V2 - Filters


## Blackbox

Here is an overview of the vibration distribution across all 3 axes on the JeNo Pocket V2 Classic. This is the **unfiltered** gyro signal from a tuning flight with Gemfan 2520-3 props:

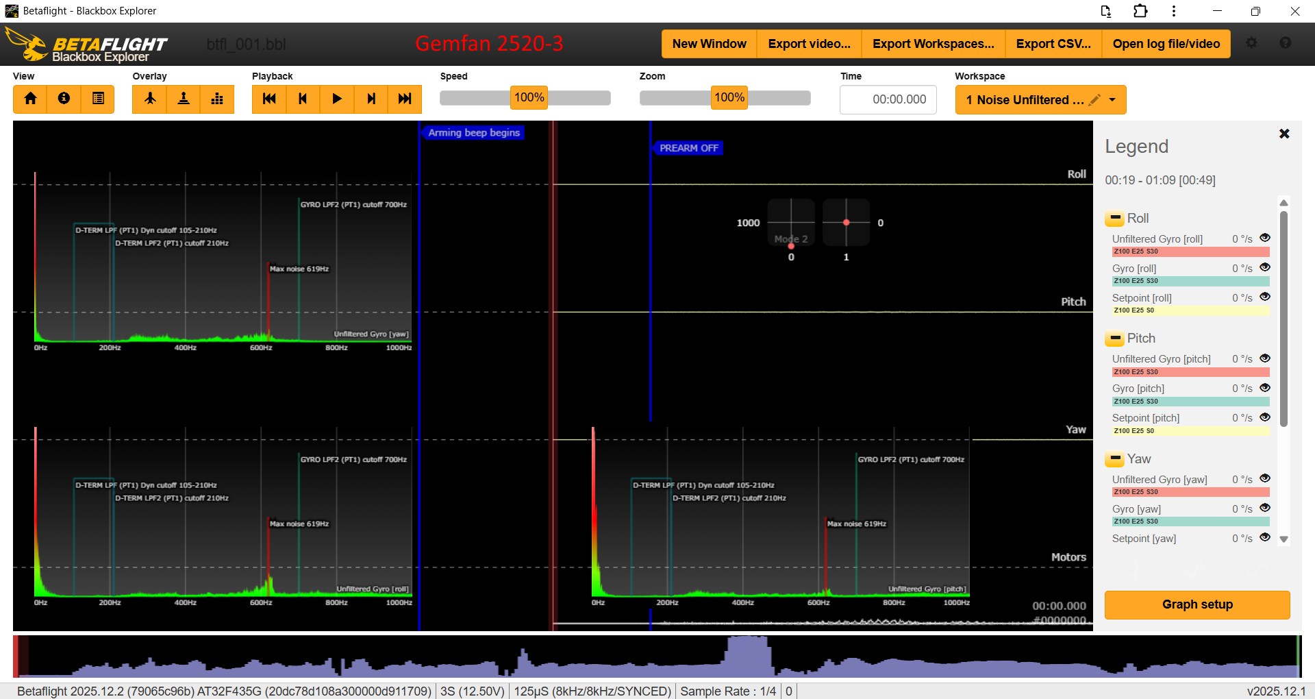
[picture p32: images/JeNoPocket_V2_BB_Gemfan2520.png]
JeNo Pocket V2 Blackbox


## Videos
Presentation of the **JeNo Pocket V2** on the **WE are FPV** channel :

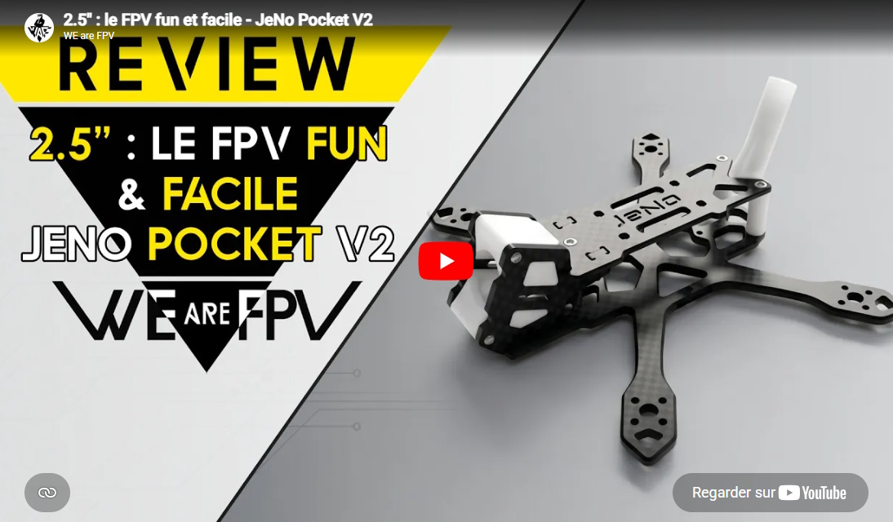
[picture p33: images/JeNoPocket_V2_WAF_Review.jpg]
JeNo Pocket V2 review on WE are FPV (French) (https://www.youtube.com/watch?v=tU0u5SXDFEE "JeNo Pocket V2 review on WE are FPV (French) - Click to Watch!")


Demonstration of the **JeNo Pocket's capabilities** :

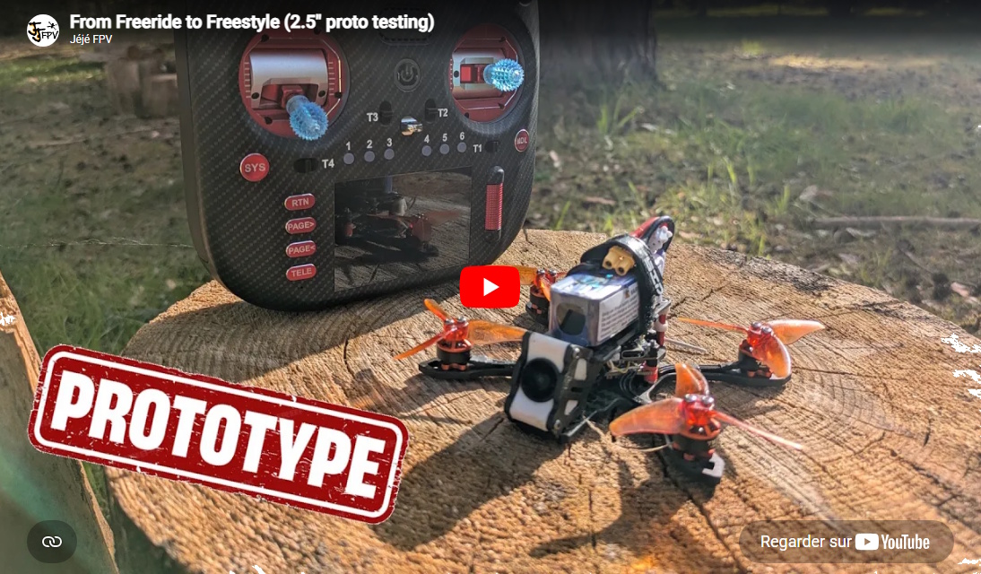
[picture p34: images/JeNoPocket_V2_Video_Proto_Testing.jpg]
JeNo Pocket V2 Freeride to Freestyle (https://www.youtube.com/watch?v=INSy-MZBwRk "JeNo Pocket V2 Freeride to Freestyle - Click to Watch!")


## Builds examples

You can find many build examples on [WE are FPV's DroneBuilds](https://forum.wearefpv.fr/71-dronebuilds/) and [RotorBuilds](https://rotorbuilds.com) :

* fr : [JeNo Pocket V2 Low Cost](https://forum.wearefpv.fr/topic/26226-jeno-pocket-v2-low-cost/) (by Jéjé FPV)
* fr : [JeNo Pocket V2 Premium)](https://forum.wearefpv.fr/topic/26227-jeno-pocket-v2-premium/) (by Jéjé FPV)
* ...

Find numerous examples of builds on the _**DroneBuilds**_ page of WE are FPV.
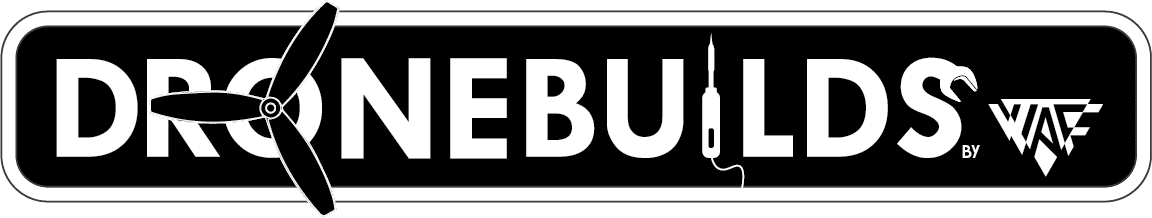
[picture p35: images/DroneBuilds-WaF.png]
DroneBuilds (https://forum.wearefpv.fr/71-dronebuilds/ "DroneBuilds - Click to Access!")


## Authors

The JeNo Pocket V2 was designed by :

* nochamo - [Youtube](https://www.youtube.com/user/nochamo)
* Jerome / Jéjé FPV - [Youtube](https://www.youtube.com/@jejefpv)
* Cam.Traveler

## TPU

Among the downloadable files, you will find several TPU parts for your JeNo Pocket V2:

* Camera TPU mounts — O4 Lite, O4 with O3 Lens Mod, and O4 Wide
* VTX antenna mounts
* Arm guards
* Rear bumper

## Community (remixes and TPU)

**Fork/remix**

If something about the JeNo Pocket V2 does not suit you 100%, feel free to take a look at the community remixes — you might find exactly what you need there:

Coming soon...

**TPU**

* [TPU set for the JeNo Pocket V2](https://www.printables.com/model/1750173-jeu-de-tpu-pour-jeno-pocket-v2) by [AltiChoco FPV](https://www.printables.com/@Nono31_454985)
* [Backpack and lipo straps](https://www.printables.com/model/1794743-jeno-pocket-lipo-strap-2s-3s-with-balance-backpack) by [Alexis Germain](https://www.printables.com/@AlexisGermai_4588665)

## Changelog

> [!TIP]
> Compatibility is consistently maintained between each version: if your frame was a v1, the parts from v1.2 will be compatible. The same applies to TPU accessories. That's why we don't keep the history of previous versions.

* Version **2.1.0** (25/07/2026) :
  * Added dedicated camera plates for the DJI O4 Wide (an entire section has been added : [DJI O4 Wide camera plates](#Camera-plates-dji-o4-wide))
  * Added slight reinforcement to the rear of the camera plates
* Version **2.0.0** (01/06/2026) :
  * Release of the JeNo Pocket V2

## Join the JeNo family !

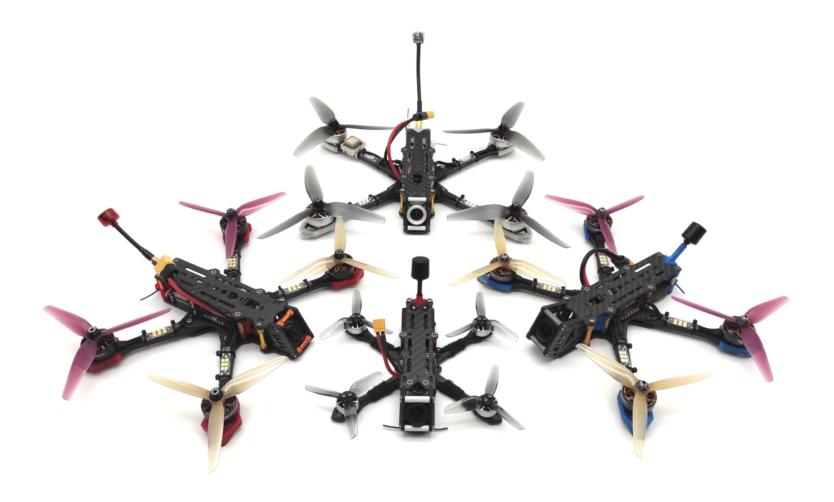
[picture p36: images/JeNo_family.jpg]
WE are FPV banner
||
|:---:|
| JeNo Classic Modus (left), JeNo Cine (right), JeNo 6" (top), JeNo 3" (bottom) |

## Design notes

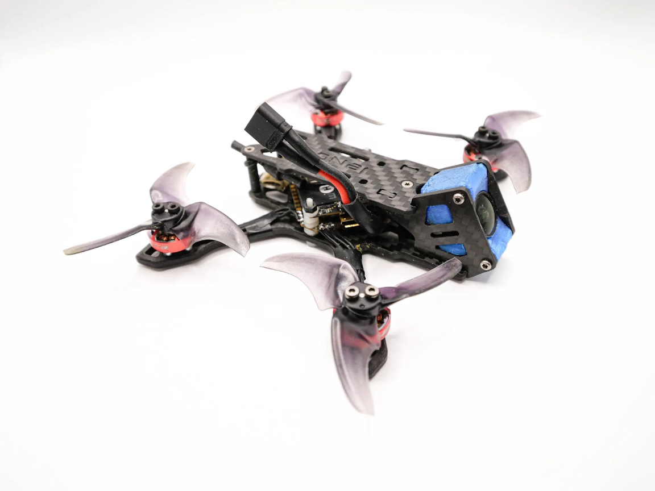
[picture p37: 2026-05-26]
images/JeNoPocket_V2_Photo_4.jpg

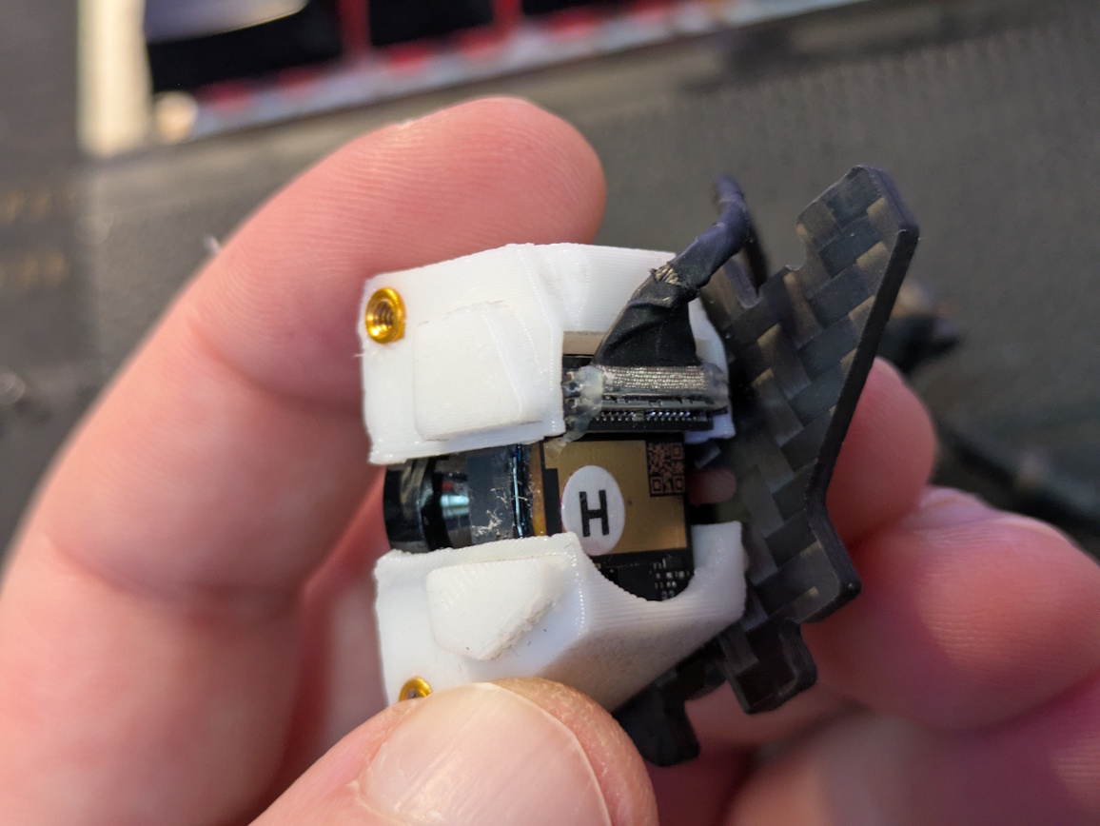
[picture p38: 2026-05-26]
images/JeNoPocket_V2_TPUçMod_O3.jpg

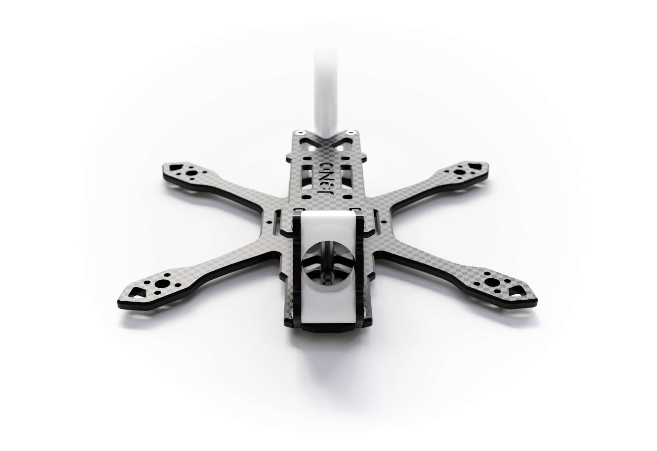
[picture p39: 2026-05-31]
images/JeNoPocket_V2_TPU_Front.jpg

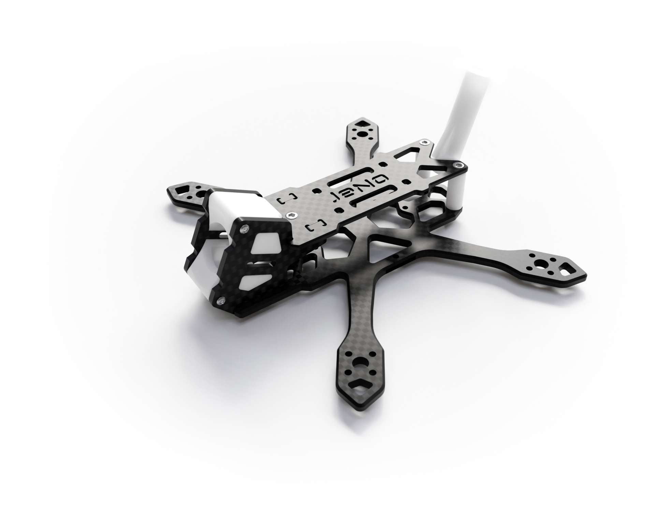
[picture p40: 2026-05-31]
images/JeNoPocket_V2_TPU_Profile.jpg

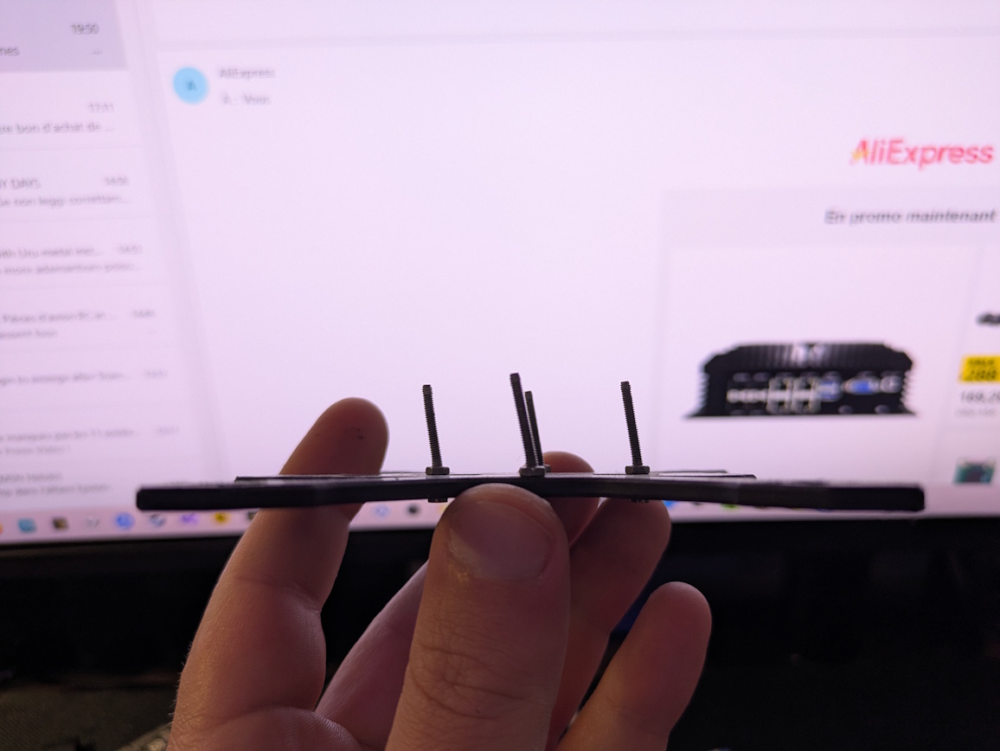
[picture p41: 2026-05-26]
images/JeNoPocket_V2_Bent_screws.jpg

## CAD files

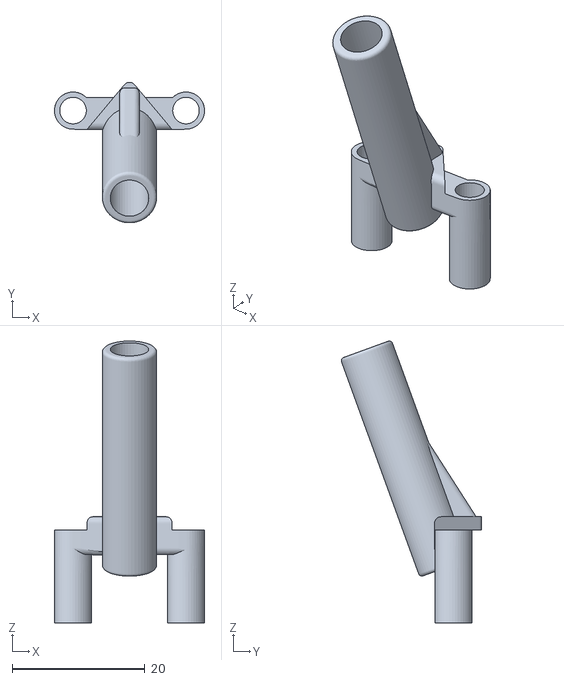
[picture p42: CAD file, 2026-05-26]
02-TPU/JeNoPocket_V2_VTX_Antenna_Full.stl
22.6 x 21.1 x 42.5

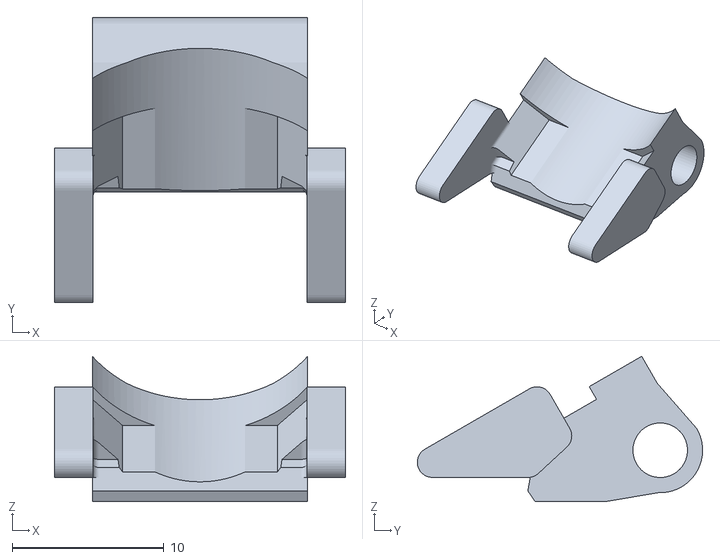
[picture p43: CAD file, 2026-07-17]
02-TPU/JeNoPocket_V2_O4_Wide_Flywoo_Bottom.stl
19.2 x 18.8 x 9.59

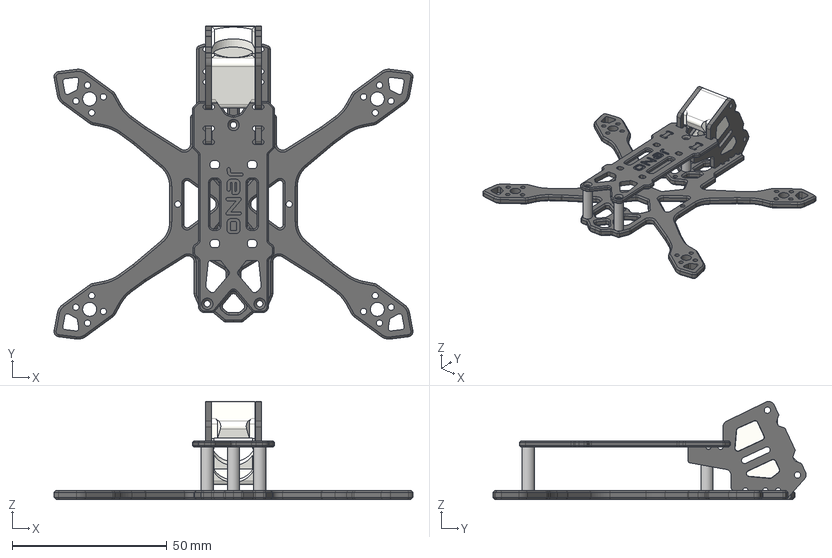
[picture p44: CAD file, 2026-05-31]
01-FRAME/JeNoPocket_V2.step
116.2 x 101.4 x 31.8 mm

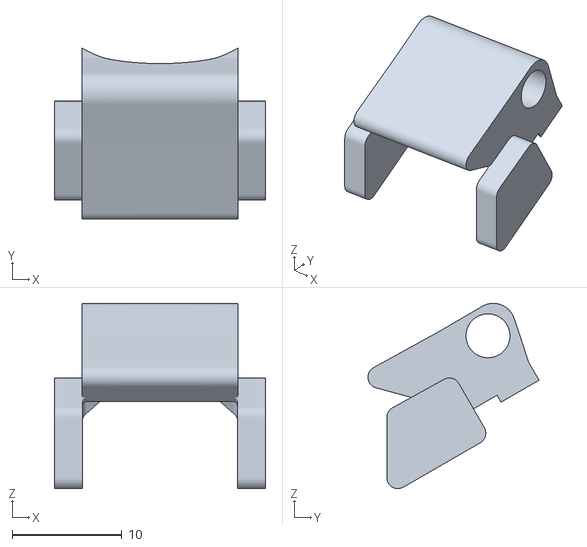
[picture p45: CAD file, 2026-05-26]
02-TPU/JeNoPocket_V2_O4_Wide_Flywoo_Top.stl
19.2 x 15.6 x 16.9

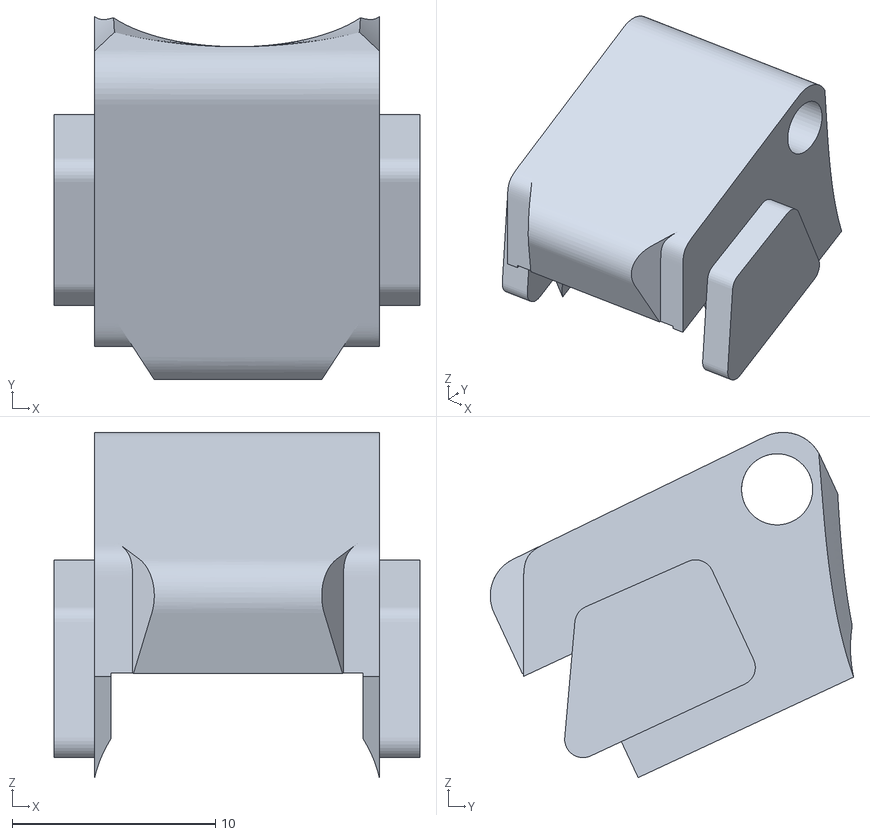
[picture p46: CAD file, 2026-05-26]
02-TPU/JeNoPocket_V2_LensMod_O3_Top.stl
18.0 x 17.9 x 17.0

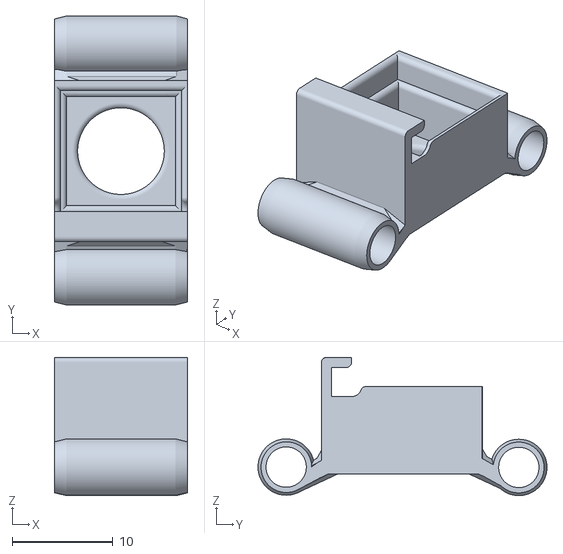
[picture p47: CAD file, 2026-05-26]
02-TPU/JeNoPocket_V2_O4_Lite.stl
13.2 x 28.7 x 13.7

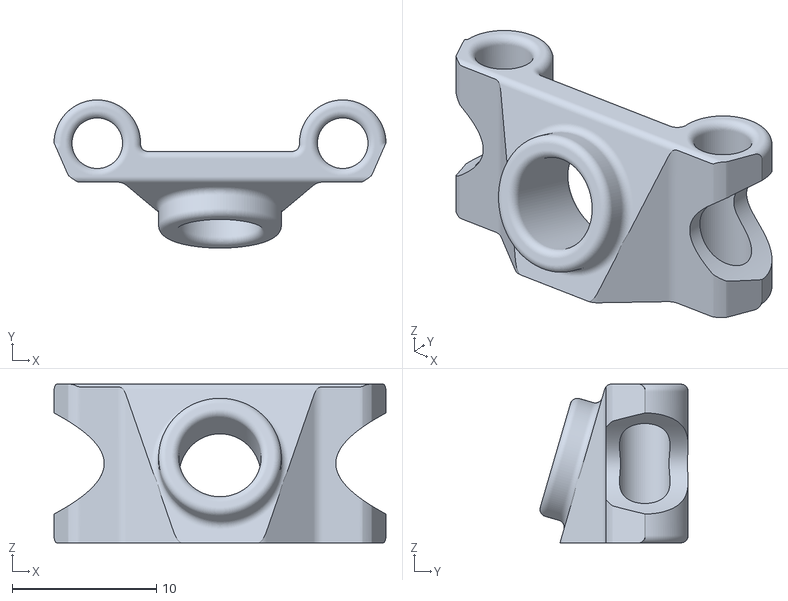
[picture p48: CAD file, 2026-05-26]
02-TPU/jenopocket_V2_VTX_Antenna_Lite_Diameter_5.5mm.stl
23.0 x 10.3 x 11.0

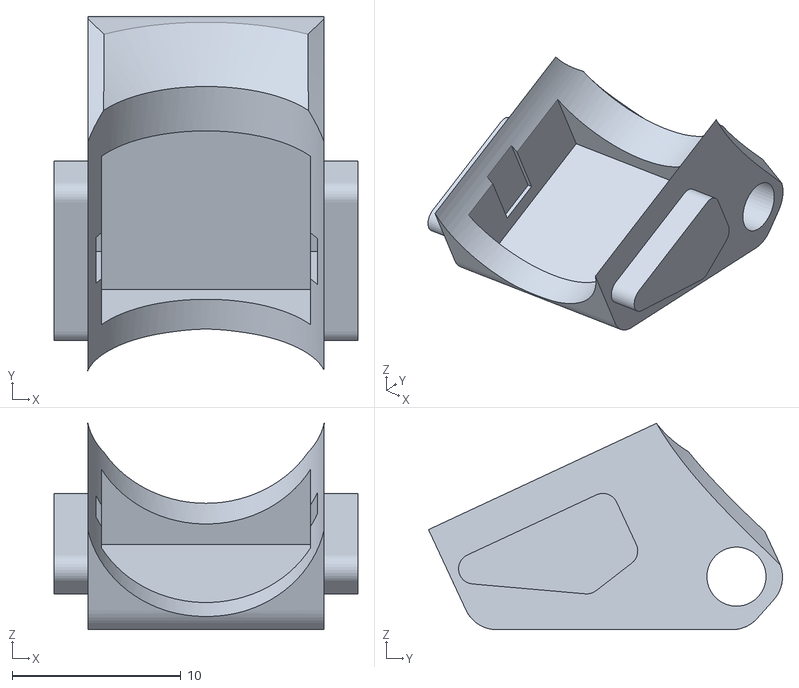
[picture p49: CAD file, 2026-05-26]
02-TPU/JeNoPocket_V2_LensMod_O3_Bottom.stl
18.0 x 21.0 x 12.2

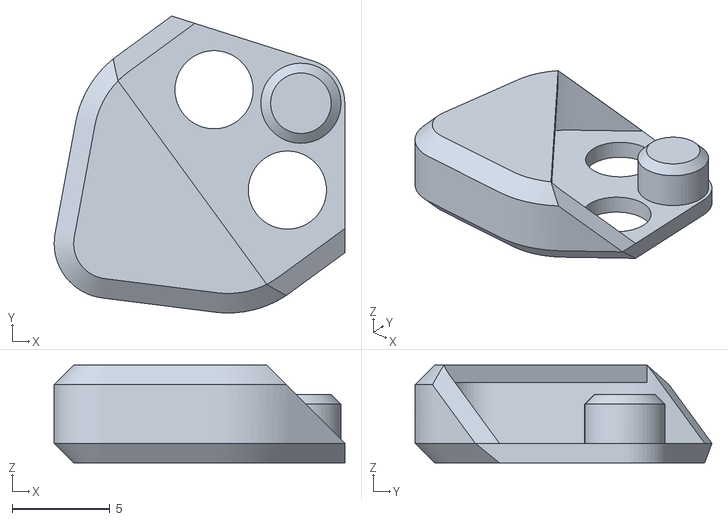
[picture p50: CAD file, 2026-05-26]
02-TPU/JeNoPocket_V2_Arm_Bumper.stl
14.9 x 15.2 x 5.00

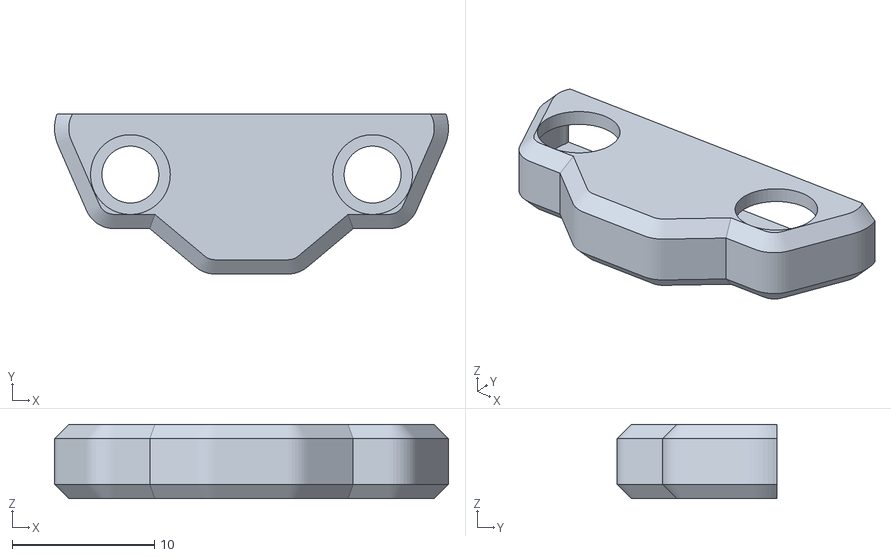
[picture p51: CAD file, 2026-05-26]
02-TPU/JeNoPocket_V2_Back_Bumper.stl
27.7 x 11.2 x 5.20

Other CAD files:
01-FRAME/JeNoPocket_V2_ALL_VERSIONS_2.1.0.dxf
03-FRAME-HISTORY/JeNoPocket_V2_ALL_VERSIONS_2.0.0.dxf
02-TPU/jenopocket_V2_VTX_Antenna_lite_Diameter_5.0mm.stl
01-FRAME/JeNoPocket_V2.stl

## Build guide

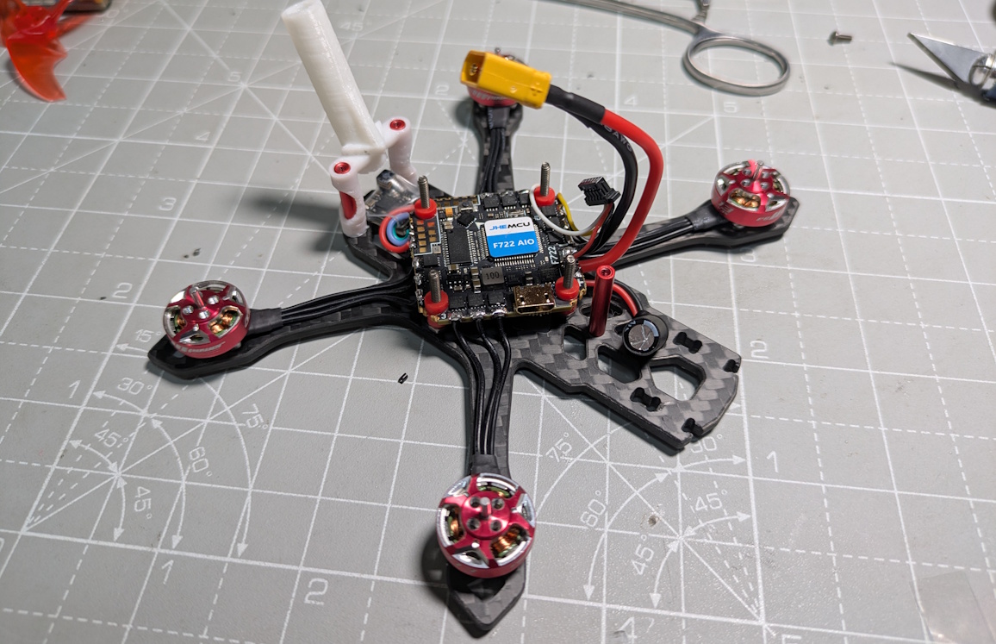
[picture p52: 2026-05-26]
images/JeNoPocket_V2_build_FC.jpg

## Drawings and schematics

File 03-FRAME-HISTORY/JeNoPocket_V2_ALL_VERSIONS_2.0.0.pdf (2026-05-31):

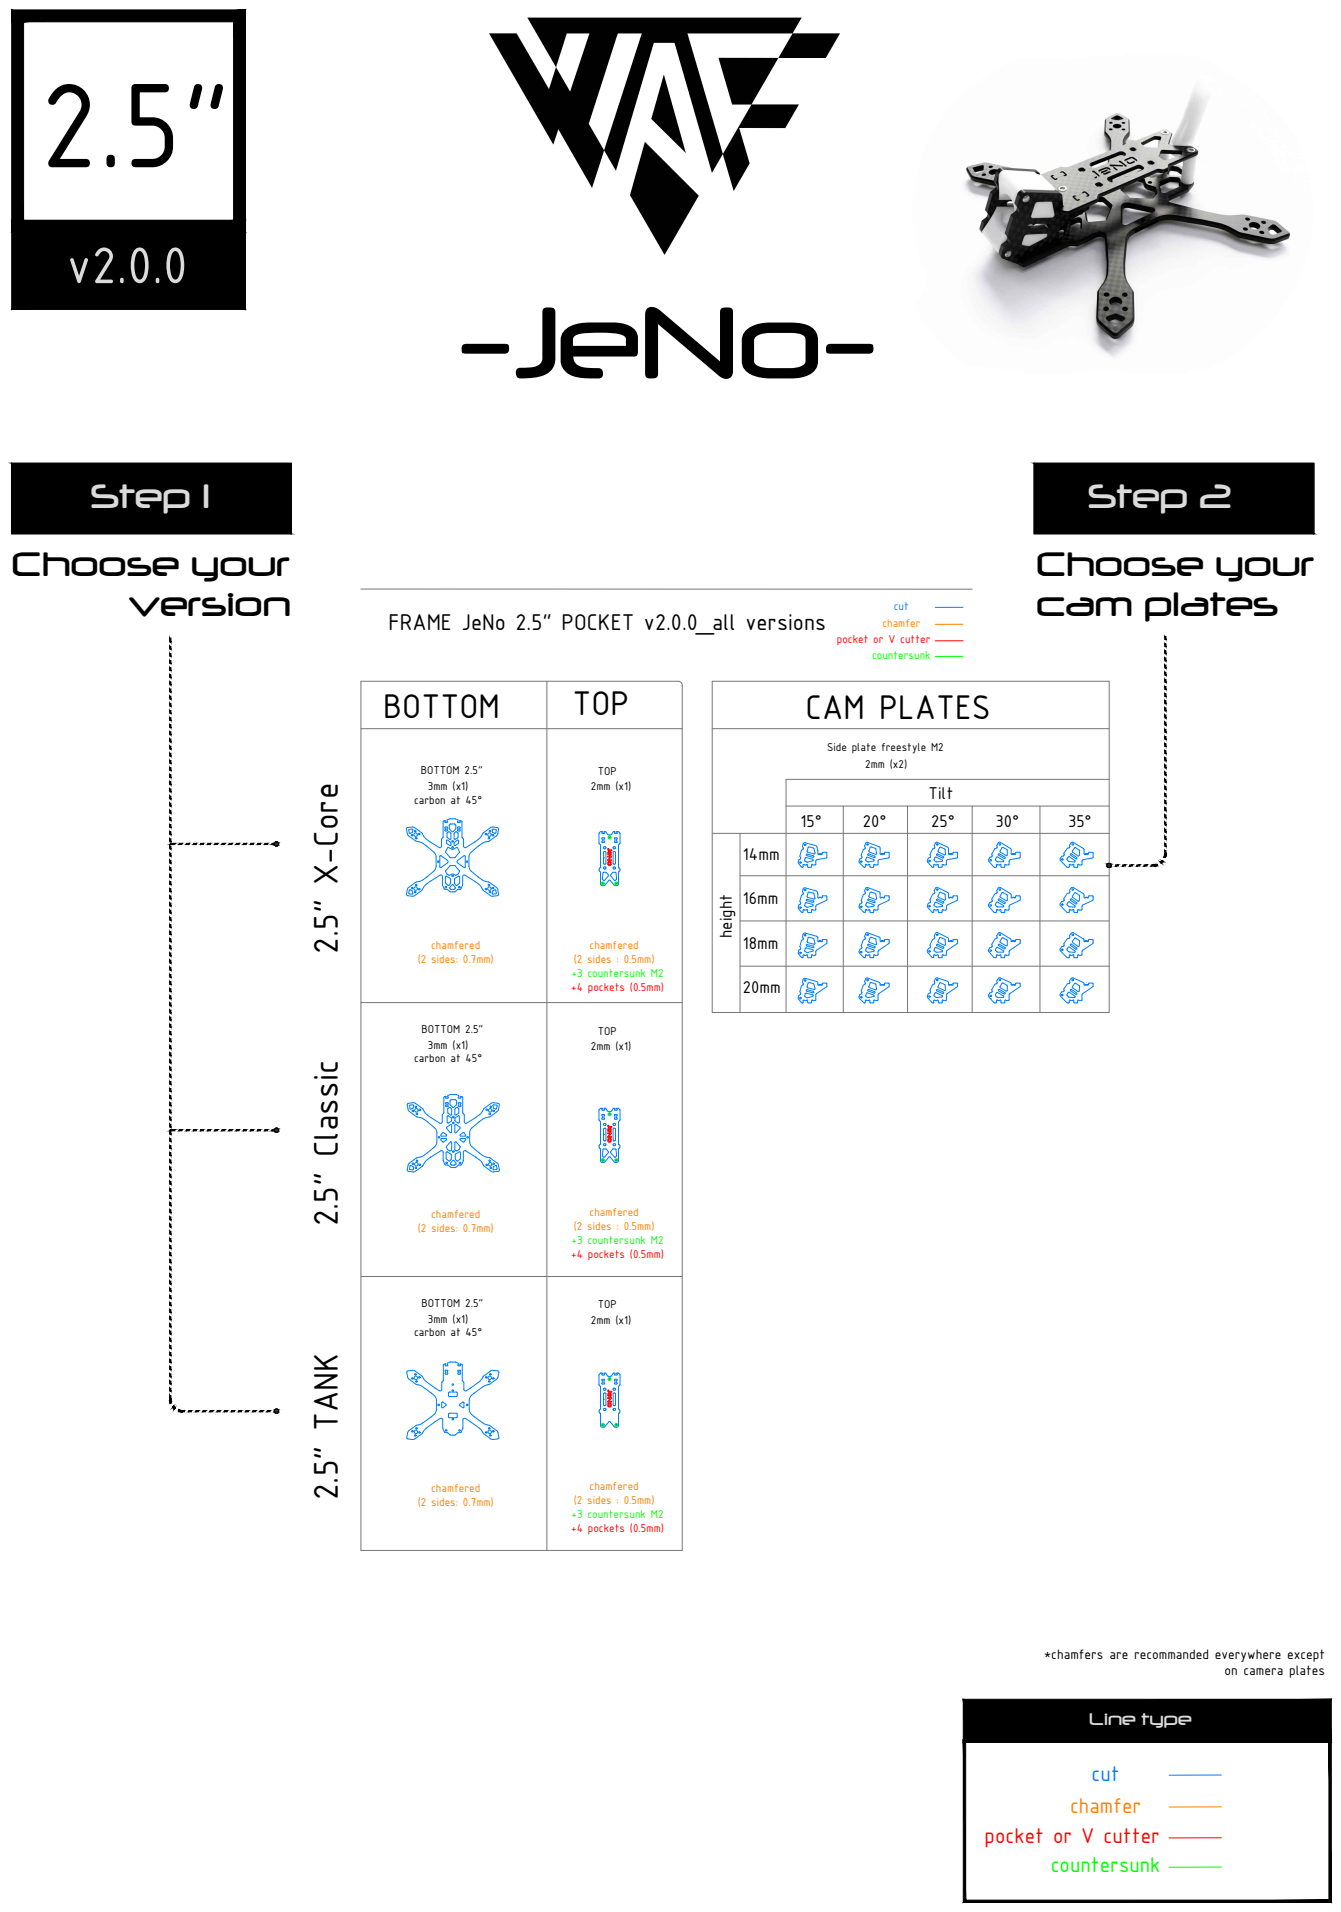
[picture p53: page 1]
3mm (x1) carbon at 45°; BOTTOM 2.5"; (2 sides: 0.7mm); BOTTOM; TOP; CAM PLATES 2.5" X-Core; (2 sides : 0.5mm) +3 countersunk M2; +4 pockets (0.5mm); height; Choose your; Choose your cam plates; Step 1 Step 2; Line type

FRAME JeNo 2.5" POCKET v2.0.0_all versions

pocket or V cutter

Side plate freestyle M2

BOTTOM 2.5" 3mm (x1) carbon at 45° chamfered (2 sides: 0.7mm) | chamfered TOP 2.5" Classic 2mm (x1) (2 sides : 0.5mm) +3 countersunk M2 +4 pockets (0.5mm)

BOTTOM 2.5" 3mm (x1) carbon at 45° | chamfered TOP 2.5" TANK 2mm (x1) (2 sides : 0.5mm) +3 countersunk M2 +4 pockets (0.5mm)

*chamfers are recommanded everywhere except

on camera plates

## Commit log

2026-05-26 Init
    Init
    [JeNoPocket_V2_ALL_VERSIONS_2.0.0.dxf]
2026-05-27 adds 3d models
    [JeNoPocket_V2.step, JeNoPocket_V2.stl]
2026-05-27 holes on top plates
    [JeNoPocket_V2_ALL_VERSIONS_2.0.0.dxf]
2026-05-31 maj visuels
    [JeNoPocket_V2.step, JeNoPocket_V2.stl]

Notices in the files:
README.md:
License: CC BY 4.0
